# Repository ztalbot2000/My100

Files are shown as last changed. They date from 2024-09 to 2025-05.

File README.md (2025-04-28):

<div class="image123">
   <div style="float:left;margin-right:5px;">
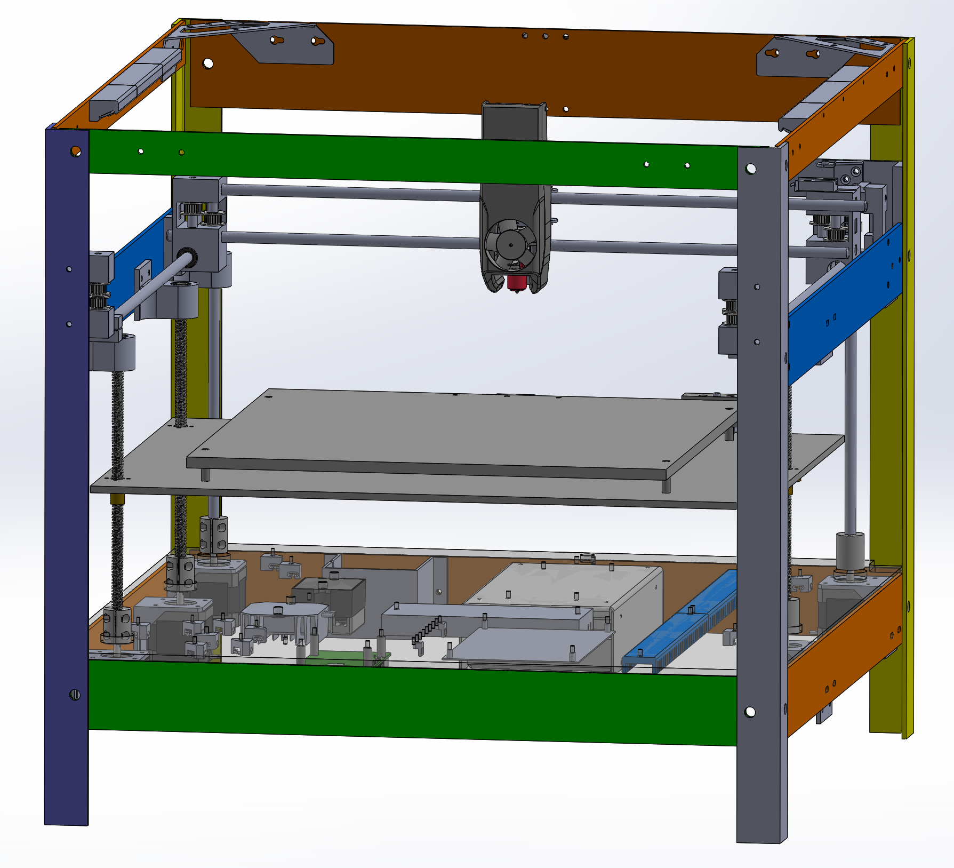
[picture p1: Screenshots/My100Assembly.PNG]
      
      <p style="text-align:center;">Latest Assembly Drawing</p>
   </div>
   <div style="float:left;margin-right:5px;">
      
      <p style="text-align:center;">Latest Build Progress</p>
   </div>
   <div style="float:left;margin-right:5px;">
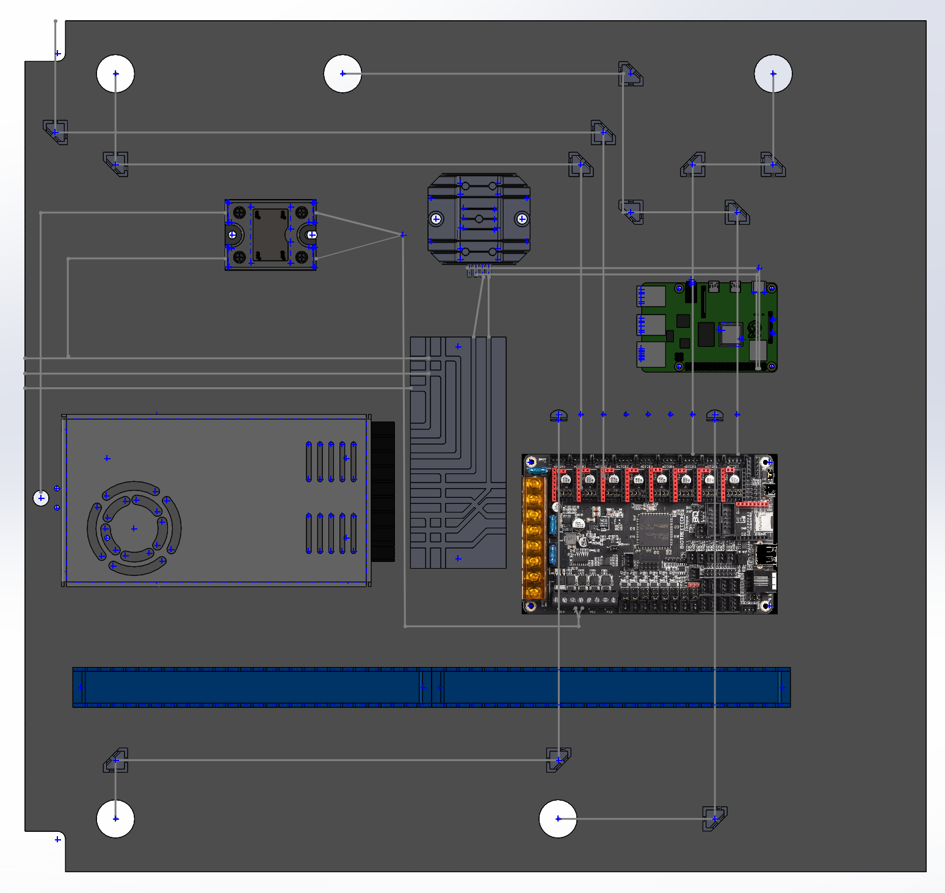
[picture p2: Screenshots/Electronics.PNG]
      
      <p style="text-align:center;">Latest Electronics Assembly Drawing</p>
   </div>
   <div style="float:left;margin-right:5px;">
      
      <p style="text-align:center;">Latest Electronics Build Progress</p>
   </div>
</div>

# My100 - A version of the100 with a metal frame.

<BR><BR>
## &nbsp;&nbsp;&nbsp; The **My100** is a meant to be built using common metal materials for a frame instead of the more expensive 20/20 extruded aluminum of the Voron or 3D printed frame of the100. This project is based primarily upon the great work of <A HREF="https://github.com/MSzturc/the100">the100</A>.
## &nbsp;&nbsp;&nbsp; BEWARE THIS WORK IS IN PROGRESS !! This is my second complete rebuild. The first failed quad gantry leveling so I decided to start again. You can see what I have created so far and are more than welcome to contribute. At the moment its just getting ready to try its first print. Wish me luck!
## &nbsp;&nbsp;&nbsp; Will the My100 be faster than the100, We shall see.

<BR><BR>
## Table of Contents
* [**My100 3D Printer Build Advantages**](#my100-3d-printer-build-advantages)
* [**Design Strategy**](#design-strategy)
* [***Imperial/Metric and Metal Thickness***](#imperialmetric-and-metal-thickness)
* [**SolidWorks 2023 Maker Edition and Equations**](#solidworks-2023-maker-edition-and-equations)
* [**Current Build Status My100 1.0 Alpha 7**](#current-build-status-my100-10-alpha-7)
* [**Current Build Status My100 1.0 Alpha 6**](#current-build-status-my100-10-alpha-6)
* [**Current Build Photos**](docs/CurrentBuildPhotos.md)
* [**ChangeLog**](CHANGELOG.TXT)
* [**Bill of Materials**](docs/My100BOM.md)
* [**Gotchas of building your own 3D printer**](docs/Gotchas.md)
* [**Contributing**](#contributing)

<BR><BR>
## My100 3D Printer Build Advantages
&nbsp;&nbsp;&nbsp; Here are some of what I believe to be My100 improvements.
<UL>
<LI>Use cheaper 6061 "L" shaped aluminum for the frame.
<LI>Wider 350 X 350mm build plate.
<LI>Keep threaded rod for Z-Axis so bed remains at height when powered off and is a less complicated assembly than gears/belts and pulleys.
<LI>Use 5mm steel shaft instead of M5 screws to support gantry bearings, eliminating noise and possible wear.
<LI>Use 20T pulley instead of F695 bearings. These seem to be higher quality. They run smoother around the 5mm steel shaft than a M5 machine screw.
<LI>All parts to be created are fully defined in SolidWorks and have been designed with equations.
<LI>Fastening holes for an enclosure is mandatory feature. Any fumes from a 3D printer should be externally vented as they are extremely harmful.
<LI>Build plate is 350 X 350mm. The height is at 200mm as I prove in the design, but is easily changed via equations of VSLength.
<LI>End stops and some sort of probe for bed leveling will be added as if you ever used a cheap 3D printer, leveling can be a nightmare.
<LI>Gantry steppers moved from within frame to electronics below so steppers will not be susceptible to heat issues.
</UL>
<BR><BR>

## Design Strategy
&nbsp;&nbsp;&nbsp; the100 is a great 3D printer otherwise I would not want to attempt to create one in the first place. It is also open source, as is the Voron. An inexpensive metal frame is the first goal.

&nbsp;&nbsp;&nbsp;20/20 extruded aluminum is expensive. Using more common 6061 "L" shaped aluminum is 50% cheaper. Just printing the100 with a 265x265mm bed was going to cost as of Oct 6/2023 $823 Cdn + tax. The aluminum for the frame of the My100 was $172 Cdn, including tax, plus $362 including tax for the Gantry blocks, larger 350 X 350mm bed, rod stabilizers and belt tensioners. Overall a much cheaper option with strength benefits. Further cost savings could be obtained if you created the bed out of metal too, but I splurged on a colorful bed.

&nbsp;&nbsp;&nbsp;Surprisingly, the ability to adjust location of parts is key and the primary reason for the second rebuild. Using ready mount stepper mounts turned out to be wiser than using the CNC to put the holes into the frame itself.

### Imperial/Metric and Metal Thickness
&nbsp;&nbsp;&nbsp;Important: In Canada metal is still purchased in Imperial units. While lengths can be obtained in Metric, the thickness would still be 1/8th inches (.125in). The .125in thickness is used throughout the design, but otherwise Metric is used.

<BR><BR>
## SolidWorks 2023 Maker Edition and Equations
&nbsp;&nbsp;&nbsp; SolidWorks Maker Edition is a fantastic tool and at $10 month its well worth it. You can stop the license at any time to save you money. I found it prettyy easy to use and there are so many tutorials out there.

### Globals WorkAround
&nbsp;&nbsp;&nbsp;There is one issue I have with the SolidWorks Maker edition and that is it does not include support for global variables being read in from a file for multiple parts. This is extremely annoying as many parts share the same equations when calculating the position of corresponding holes.

&nbsp;&nbsp;&nbsp;To that end I created a Node.js tool called <A HREF="https://github.com/ztalbot2000/SWECompare">SWECompare (SolidWoreks Equation Comparison)</A> to help with the task of having multiple parts use the same equations. 
<BR>

### Understanding the Equations
&nbsp;&nbsp;&nbsp;To change the dimensions of this 3D printer or to know how it was designed, you must understand the underlying equations.

#### Vertical alignment
&nbsp;&nbsp;&nbsp;Each component is stacked relative to the other, in the following manner.

<UL>
<LI>Electronics below the lower rail.
<LI>The length of the Z-Axis threaded rods at the end of the steppers.
<LI>The bed at the top of the Z-Axis.
<LI>The build plate on top of the bed.
<LI>The tip of the hotend on the build plate equal to the build plate on top of the bed.
<LI>The middle of the top the X-Axis rod from the hot end tip..
<LI>The middle of the Y-Axis rod from the middle of the X-Axis rod.
<LI>The middle of the X-Axis rod to the top pulley of the gantry.
</UL>

#### Left to Right Alignment.
&nbsp;&nbsp;&nbsp;It is not the build plate that dictates the width but the length of the X-Axis linear rod so it fits between the left and right gantry blocks. The bed and build plate are then centered between the steppers in this direction.

#### Front to Back Alignment
&nbsp;&nbsp;&nbsp;The front steppers for the Z-Axis are by the belt tensioners. The build plate size dictates everything else. Similiarly the Y-Axis linear rail placement traverses the length of the build plate so that the hot end tip can reach the whole area.

<BR><BR>
## Current Build Status My100 1.0 Alpha 7
(In progress)
<UL>
   <LI> Bed Mesh works
   <LI> Added larger Z endstop switch
   <LI> Moved gantry steppers to electronics below.
   <LI> Moved drag chain to middle of hot end carrier to remove the possability of any lever affect to the hot end.
   <LI> Trying to print... Oooooh
</UL>

<BR><BR>
## Current Build Status My100 1.0 Alpha 6
<UL>
   <LI>CAD design is complete.
   <UL>
      <LI>I was smarter in using rods as Matt pointed out when he had seen my first designs to solve flexing issues.
      <LI>Moved to Z-Tilt instead of QGL. Trying to level a four legged chair is not ideal.
      <LI>Connection points use one 8mm screw to allow for racking adjustments.
      <LI>Steppers are mounted with brackets and a slot for adjusting.
   </UL>
   <LI> Drag chains added. (Not in CAD design yet)
   <LI> Disco lights added.
   <LI> Build is complete.
   <LI> Wiring is tested. All motors move appropriately.
   <LI> All axis home.
   <LI> Automatic bed leveling complete. This was the fault with the previous design.
   <LI> Hot end heats up.
   <LI> Bed heats up.
   <LI> Working on Tidying up build, Tuning klipper config under RatOS 1.20.
</UL>

<BR><BR>
## Contributing
&nbsp;&nbsp;&nbsp; Best ways to contribute
* Star it on [GitHub](https://github.com/ztalbot2000/My100) - if you use it and like it please at least star it :)
* Follow the repo on [GitHub](https://github.com/ztalbot2000/My100)
* Follow me [ztalbot2000](https://github.com/ztalbot2000)

<BR><BR>
## Inspiration and special thanks
Based on :
* [the100]https://github.com/MSzturc/the100
* Thanks especially to those who continue to work on the100 and those who make it better.
* And most importantly my Wife.

<BR><BR>
## License
See [LICENSE](LICENSE)

<!---
Link References (Not Local)
-->

[ncviewer]:https://ncviewer.com
[viewstl]:https://viewstl.com/classic/
[Clicky Installation]:https://3dpblog.com/klicky-probe-installation-voron/
[BLTouch Installation]:https://www.klipper3d.org/BLTouch.html
[Ratrig v-core-3]:https://docs.ratrig.com/product-details/v-core3-1
[Heater Pad installation]:https://www.youtube.com/watch?v=RnCW7-_G2dI
[Heater Pad installation]:https://www.youtube.com/watch?v=-fMPnBuyxy8
[Heater Pad installation]:https://www.youtube.com/watch?v=BE1rW7XyXqw
[Heater Pad installation]:https://www.youtube.com/watch?v=yhzWj-oaikk
[Hot End Wiring Guide]:https://docs.ldomotors.com/en/voron/voron2/wiring_guide_rev_c
[Understanding End Stops]:https://www.youtube.com/watch?v=Q2uBK5XzX4I
[Macros - Ellis Tuning Guide]:https://ellis3dp.com/Print-Tuning-Guide
[Disco on a Stick]:https://github.com/VoronDesign/Voron-Hardware/tree/master/Daylight/Disco_on_a_stick
[Bigtree Octopus v1 prep and wiring]:https://www.youtube.com/watch?v=_4YpUzo18Lc
[ztalbot2000]:https://github.com/ztalbot2000

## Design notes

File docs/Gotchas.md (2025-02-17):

<p align="center">
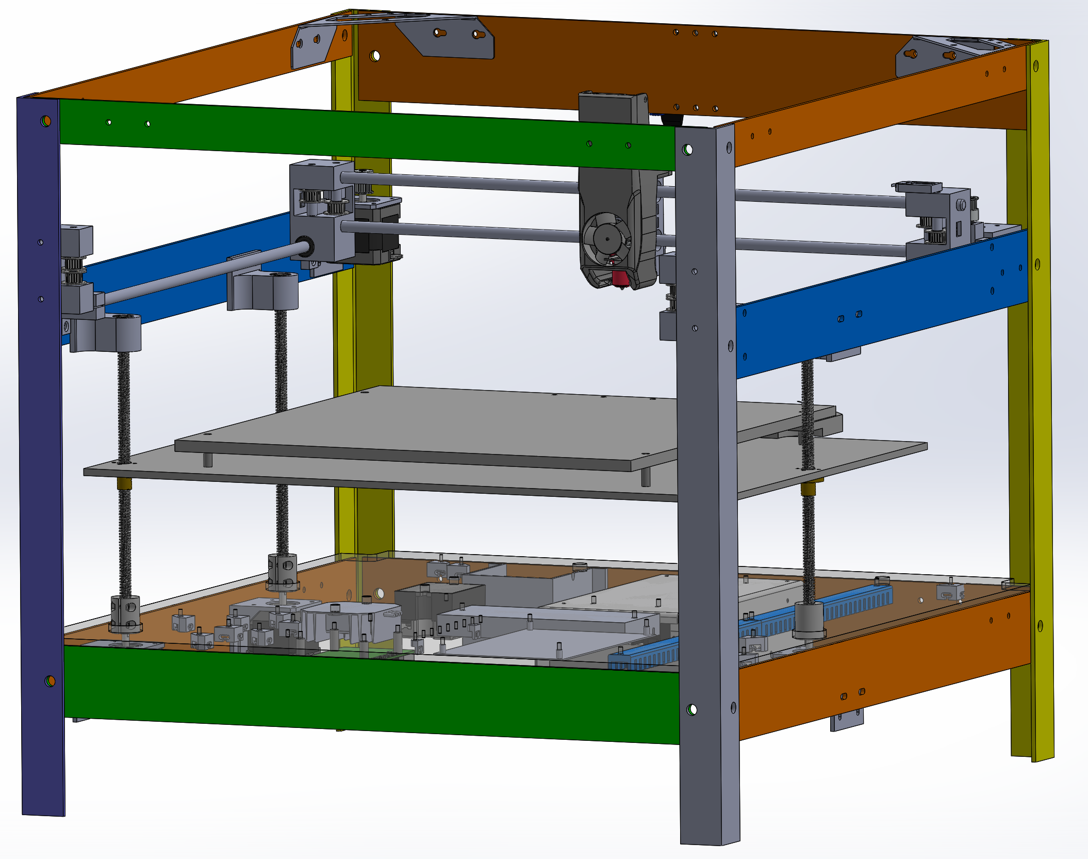
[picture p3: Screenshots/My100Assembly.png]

</p>

# These are a list of things I learned the hard way about building a 3D printer; So even if you do not build this printer, but decice to build your own, these are things to look out for.

## Leasons learned the hard way, that may not be so obvious.
<UL>
<LI> Many control boards with the same version number have different versions of STM32 controller chips. Understand and even try to compile the firmware for the control board you intend to buy. Take into consideration which stepper drivers you will be using as some firmware and even OS's say they support TMC2208 stepper drivers but only work with TMC2209. Prototyping just the controller with steppers and stepper drivers and getting them controlled by the OS of your choice will save you a lot of time and you may even understand the complexity of the whole project..
<LI> The more you design in SolidWorks, the less iterations you will have to build.
<LI> You need a 3D printer to build a 3D printer. Buying a cheap one is cheaper than having your parts printed. You will also learn how a 3D printer works and the pitfalls of a cheap one too.
<LI> JST-XH connectors are very tiny. Buy a good crimping tool and practice practice practice.
<LI> Buying steppers with connectors built into them will save you crimping some of the tiny JST-XH connectors.
<LI> A large 3D printer seems like the way to go, but it is correct that most things you will want to print can be done on a 235x235mm printer.
<LI> CoreXY printers do not have an X stepper and Y stepper because both steppers are needed to move the hot end in a single direction.
<LI> Quad Gantry Leveling refers to 4 point leveling where Z-Tilt referes to 3 points.
<LI> Trying to save money by putting the mounting holes directly into "L" shaped aluminum seemed like a good idea, but does not allow you to adjust the positioning later.
</UL>

<BR><BR>
## Wiring Gotchas
<UL>
<LI> I'll repeat this again. CoreXY printers do not have an X stepper and Y stepper because both steppers are needed to move the hot end in a single direction. So the steppers are actually Gantry Left and Gantry Right. Gantry left is Motor 1 and Gantry Right is Motor 0. Klipper still refers them to as stepper_x and stepper_y as Klipper supports many different 3D printer motion movement, but they are actually Gantry Right and Gantry Left.
</UL>

<BR><BR>
## License
See [LICENSE](../LICENSE)

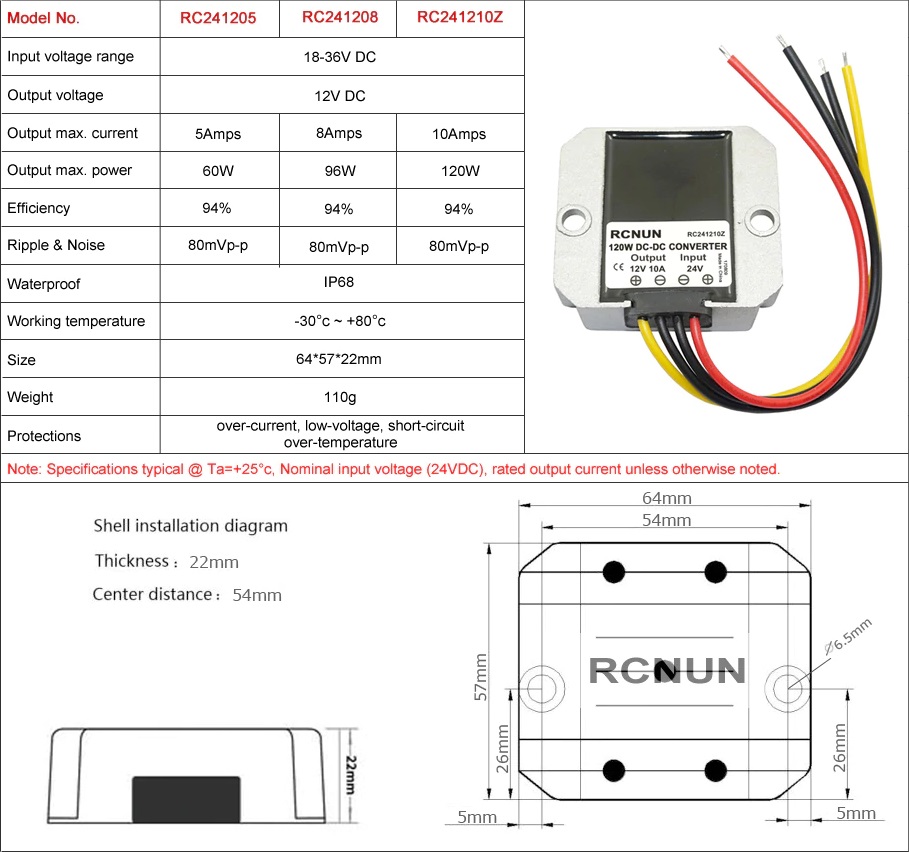
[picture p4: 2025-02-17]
SLD/AcquiredParts/RCNUN/RC2412 Spec.jpg

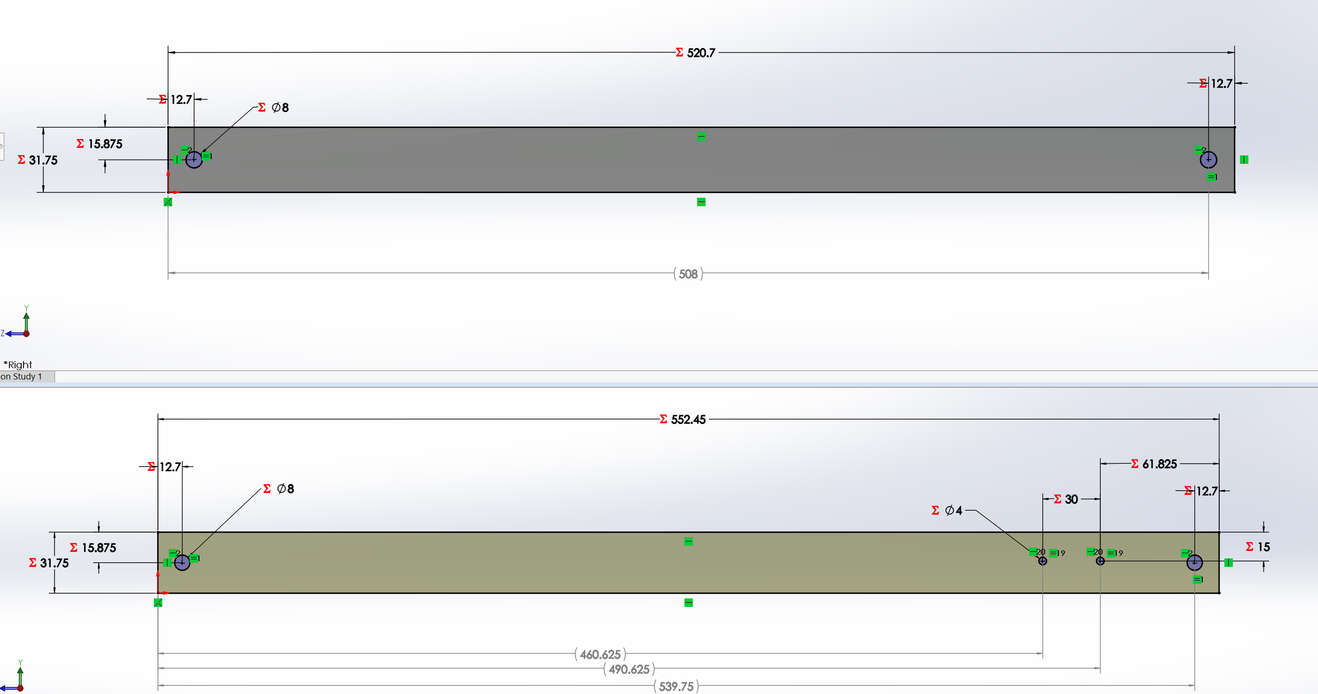
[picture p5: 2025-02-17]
Screenshots/Dimensions/UpperRails.PNG

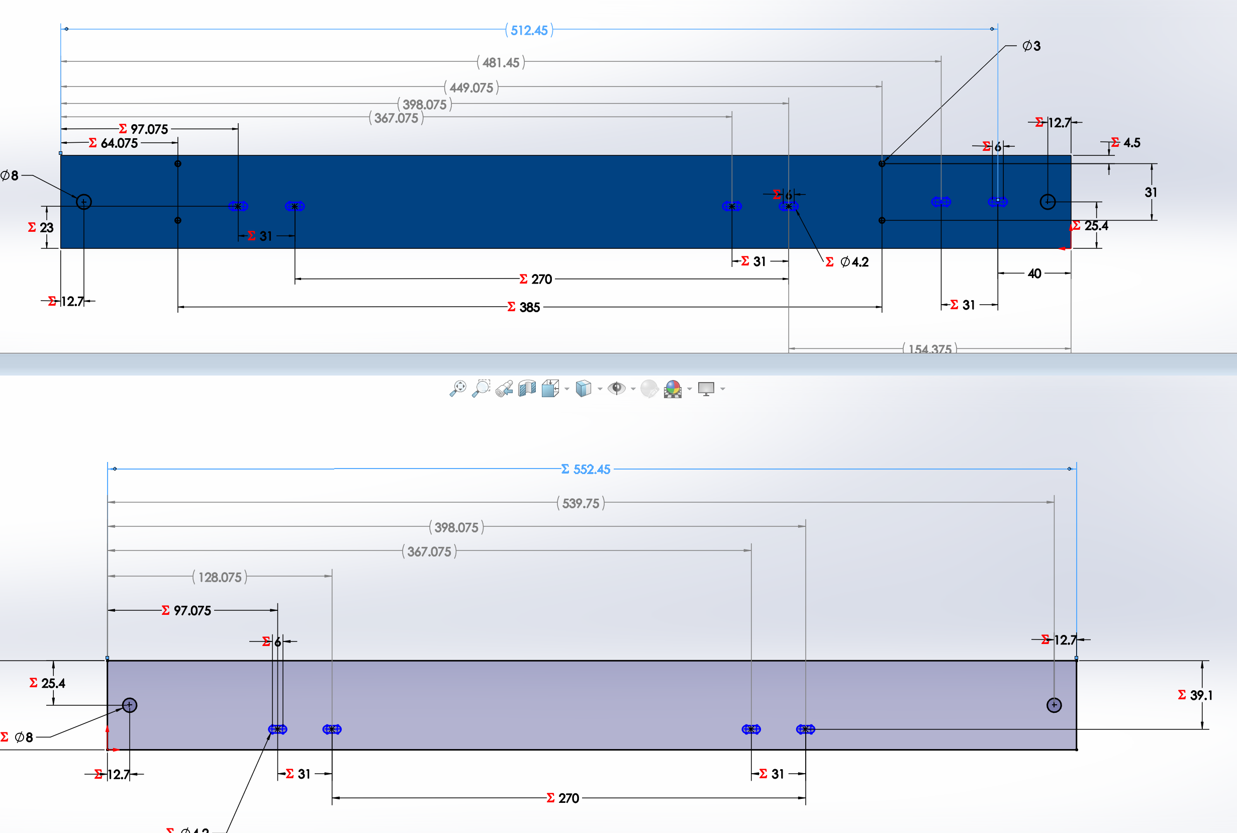
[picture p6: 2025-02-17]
Screenshots/Dimensions/LeftRails.PNG

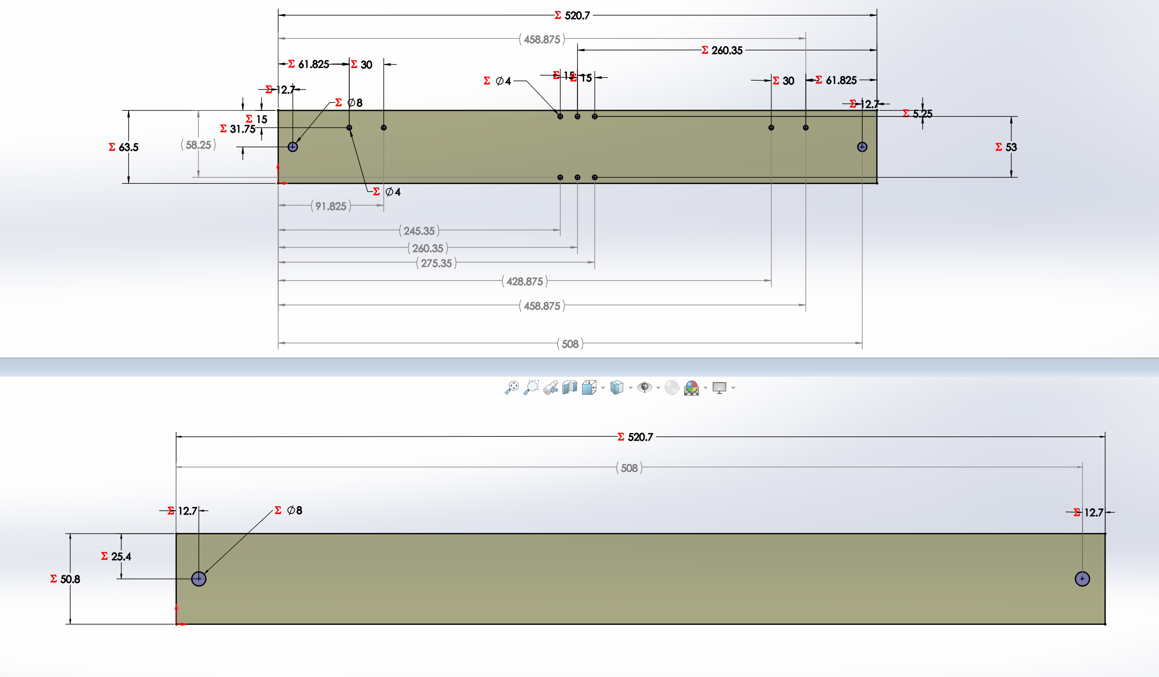
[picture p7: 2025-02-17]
Screenshots/Dimensions/FrontBackRails.PNG

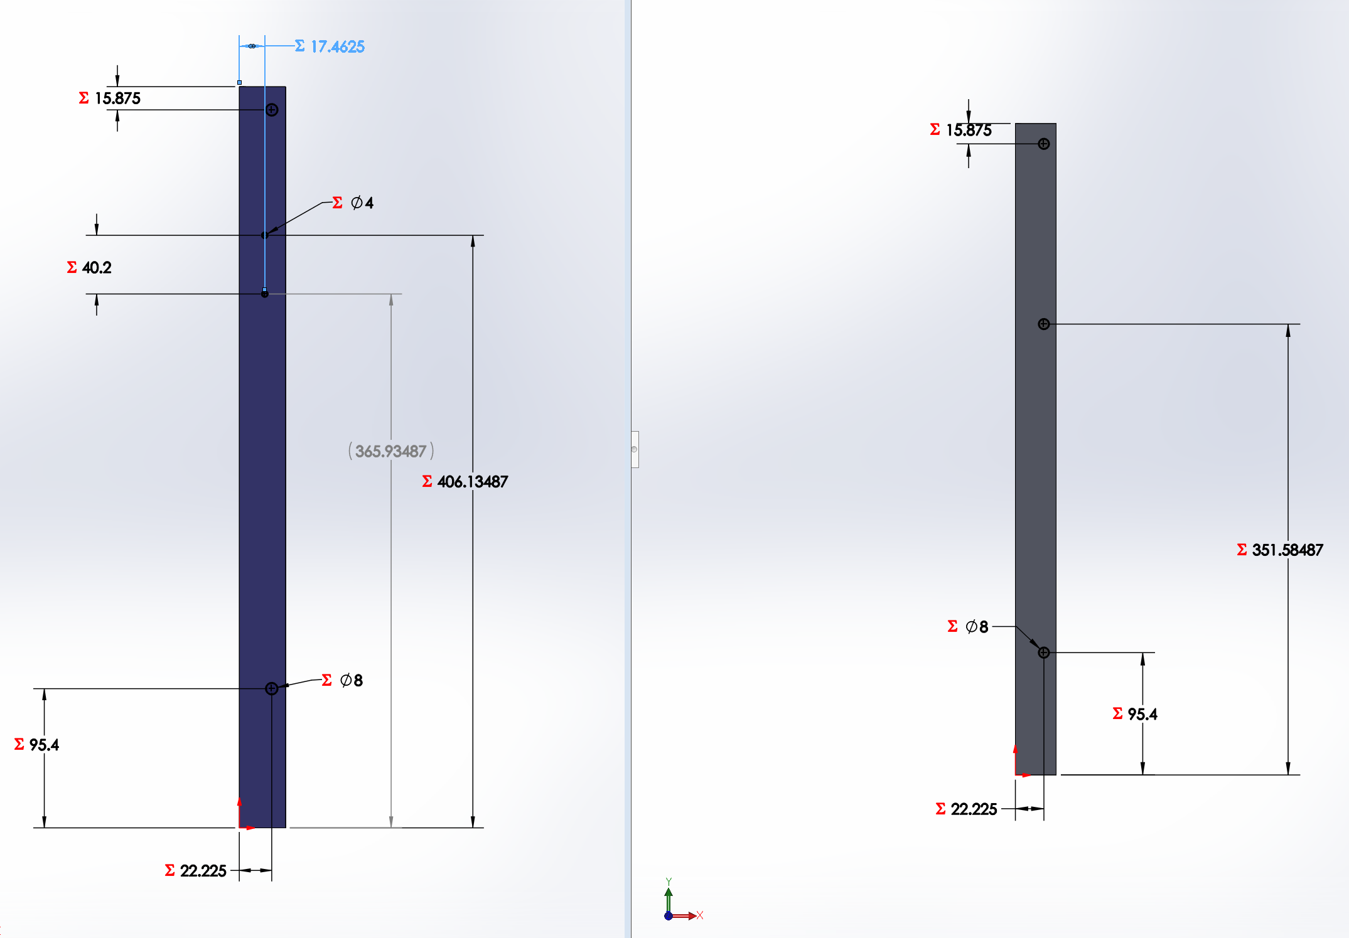
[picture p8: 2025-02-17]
Screenshots/Dimensions/FrontVS.PNG

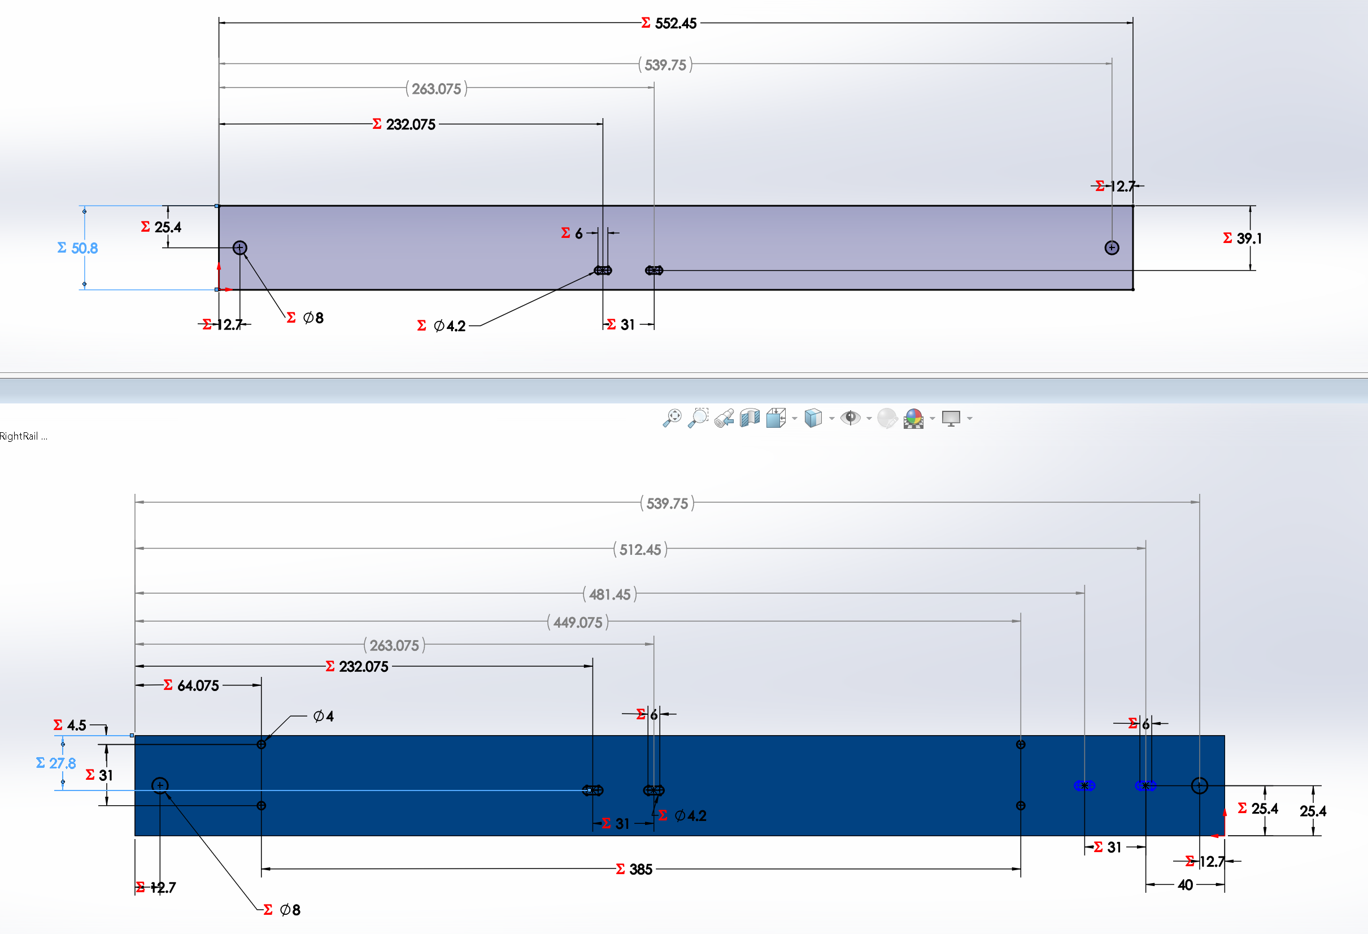
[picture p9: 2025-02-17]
Screenshots/Dimensions/MidRightAndRightLowerRails.png

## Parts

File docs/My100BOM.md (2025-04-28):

<HTML>
   <HEAD></HEAD>
   <BODY>
      <H1>Bill of Materials that differ from the100</H1>
      <TABLE>
         <HR><TD>Part<TD>Quantity<TD>Price (CDN)<TD>URL<TD>Purpose</HR>
         <TR><TD>Steel Shaft 5mm - 30mm<TD>6<TD>$2.95 each<TD>https://www.3dlabtech.ca/product/steel-shaft-5mm/<TD></TR>
         <TR><TD>Silicone Heater Mat 300mmx300mm-650w<TD>1<TD>$64.95<TD>https://www.3dlabtech.ca/product/silicone-heater-mat/<TD></TR>
         <TR><TD>PCB Klicky Probe kit<TD>1<TD>$29.95<TD>https://www.3dlabtech.ca/product/pcb-klicky-probe-kit/<TD></TR>
         <TR><TD>RJ4JP-01-08 Drylands<TD>4<TD>$4.58<TD>https://s.click.aliexpress.com/e/_DkZVosj<TD></TR>
         <TR><TD>Smooth Idler 6mm wide<TD>8<TD>$4.45 each<TD>https://www.3dlabtech.ca/product/smooth-idler-6mm-wide/<TD></TR>
         <TR><TD>Voron Trident Cast Aluminum 8mm Build Plate - 350x350mm<TD>1<TD>$164.95<TD>https://www.3dlabtech.ca/product/smooth-idler-6mm-wide/<TD></TR>
         <TR><TD>6-32 x 5/8 standard screws<TD>104<TD>$.05<TD><TD>Frame fastener</TR>
         <TR><TD>6-32 nuts<TD>104<TD>$.05<TD><TD>Frame fastener</TR>
         <TR><TD>6-32 lock washer<TD>104<TD>$.05<TD><TD>Frame fastener</TR>
         <TR><TD>M3 x 8 standard screw<TD>8<TD>$.15<TD><TD>Y axis guide block fastener</TR>
         <TR><TD>M3 x 8 pan head screw<TD>4<TD>$.15<TD><TD>Gantry rail clamp fastener</TR>
         <TR><TD>M3 x 20 standard head screw<TD>4<TD>$.15<TD><TD>X Axis guide block fastener</TR>
         <TR><TD>M4 x 25 standard head screw<TD>4<TD>$.15<TD><TD>Belt tightener fastener screws</TR>
         <TR><TD>M4 nylon nut<TD>4<TD>$.15<TD><TD>Belt tightener fastener screws</TR>
         <TR><TD>6-32 x 5/8 Cap Screw Socket Head<TD>14<TD>$.10<TD><TD>Bottom Frame Enclosure screws</TR>
         <TR><TD>6-32 Nylon Insert Hex lock nuts<TD>1<TD>$16.81 per 110<TD>https://www.amazon.ca/dp/B0CFHSM134?ref=ppx_yo2ov_dt_b_product_details&th=1<TD>Bottom Frame Enclosure screws</TR>
         <TR><TD>M6x16 Bolt<TD>2<TD>$.35 each<TD><TD>24v to 5V Power converter mounting bolts</TR>
         <TR><TD>M6 Nylon nut<TD>2<TD>$.30 each<TD><TD>24v to 5V Power converter mounting nuts</TR>
         <TR><TD>M4x10 Socket Cap screws<TD>4<TD>$.35 each<TD><TD>24v Power Supply mounting screws</TR>
         <TR><TD>Nema 17 42m Stepper Motor<TD>7<TD>$33.35 for 5<TD><TD></TR>
         <TR><TD>Mellow Hartk Sexbolt Z Limit Endstop Pcb Hardware Injection Kit Mod For Diy Voron 2.4 Trident 3D Printer<TD>1<TD>$12.28<TD>https://www.aliexpress.com/item/1005005910004587.html<TD></TR>
         <TR><TD>Disco on a Stick<TD>1<TD>$11.28 for 2<TD>https://www.aliexpress.com/item/1005005913975209.html<TD></TR>
      </TABLE>
   </BODY>
</HTML>

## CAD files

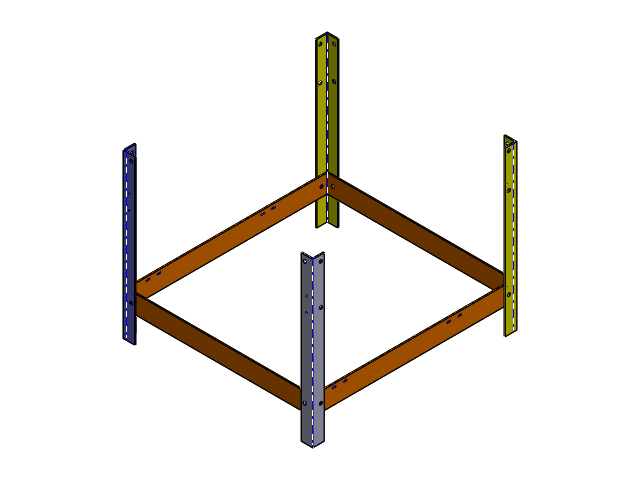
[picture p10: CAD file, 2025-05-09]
SLD/BottomFrame/My100LowerAssembly.SLDASM
FrontLeftVerticalSupport
LeftBeltTensioner
POWGE_2FT_pulley_20T_B5 x 4
7mmx1mmSpacer x 2
LowerFrontRail
FrontRightVerticalSupport
RightBeltTensioner
LowerRightRail
Nema17Mount x 5
LeadScrew 200mm x 8mm x 3
LeadScrew Nut 8mm x 2mmPitch x 3
Coupler x 5
Frontplate x 5
Backplate x 5
Connenctor x 5
Housing x 5
Bearing dummy x 5
Bearing dummy 01 x 5
Core x 5
Cable x 5
M3x34-Screw x 20
RodShaft-250mmx8mm x 2
GT2 Timing Pulley x 2
BackRightVerticalSupport
LowerBackRail
AC Power Inlet
PowerSwitchCover
BackLeftVerticalSupport
LowerLeftRail

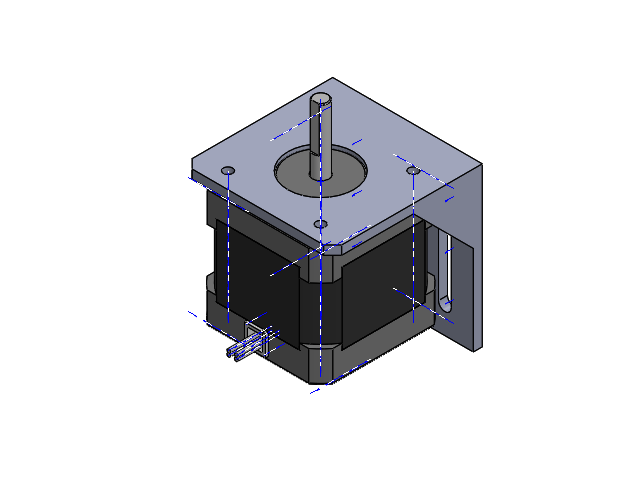
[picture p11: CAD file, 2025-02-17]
SLD/FromThe100/NEMA17-40/Nema17-40WithMountBracketAssembly.SLDASM
Nema17Mount
Frontplate
Backplate
Connenctor
Housing
Bearing dummy
Bearing dummy 01
Core
Cable
M3x34-Screw x 4

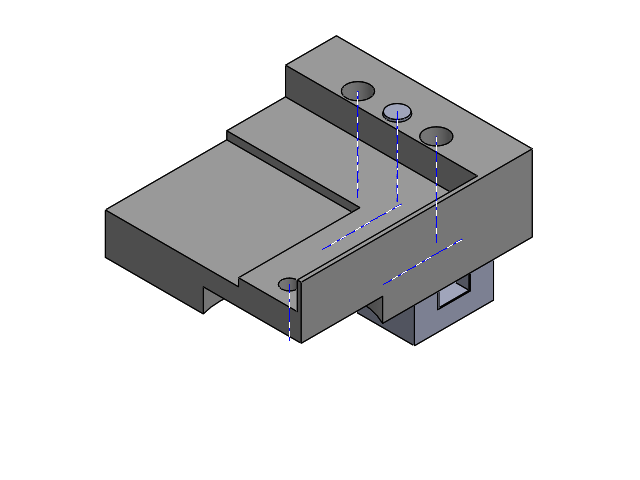
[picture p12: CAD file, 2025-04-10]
SLD/Bed/BuildPlateZEndStopHolderAssembly.SLDASM
BuildPlateZEndStopSwitchHolder
ZEndStopLimitSwitch

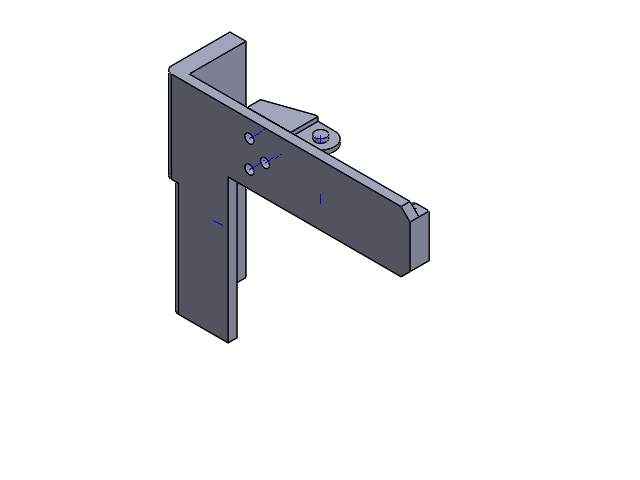
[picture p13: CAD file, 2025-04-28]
SLD/Extras/DragChainHangerAssembly.SLDASM
DragChainHanger
DragChainEndLinkMale

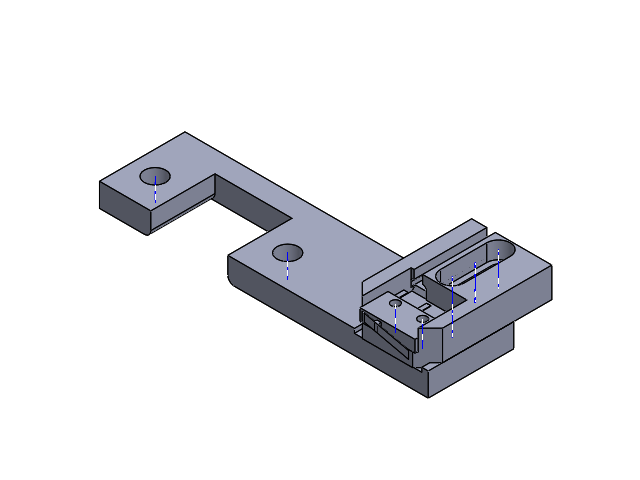
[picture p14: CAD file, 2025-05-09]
SLD/Gantry/YEndStopForRightRearSK8RodHolderAssembly.SLDASM
YAxisEndStopMicroSwitchHolder
MicroSwitch
YAxisEndStopBaseForRightRearSK8RodHolder

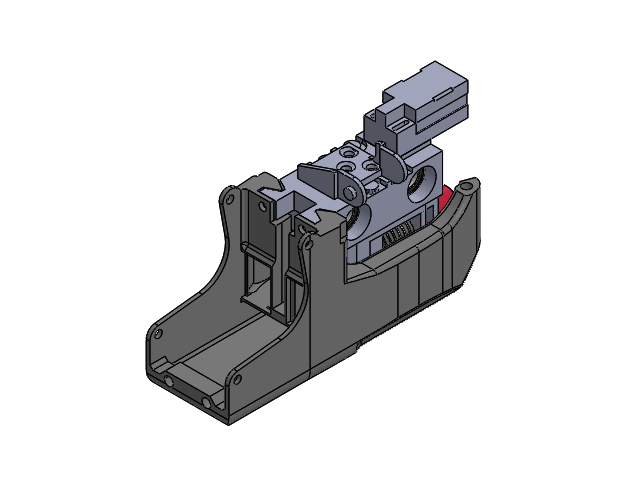
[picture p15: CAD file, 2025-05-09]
SLD/Hotend/HotEndAssembly.SLDASM
Heater
Arm
Sock
Screw_1
Hotend
Clip
Top_1
Screw
0.4 TUN Nozzle
CHC Pro Mount-17
CHC Pro Mount-18
4010 Fan Axial
Fanhead-19
CHC Mount
Carrier
InductiveProbe
LM8UU x 2
DragChainEndLinkRotatedMale

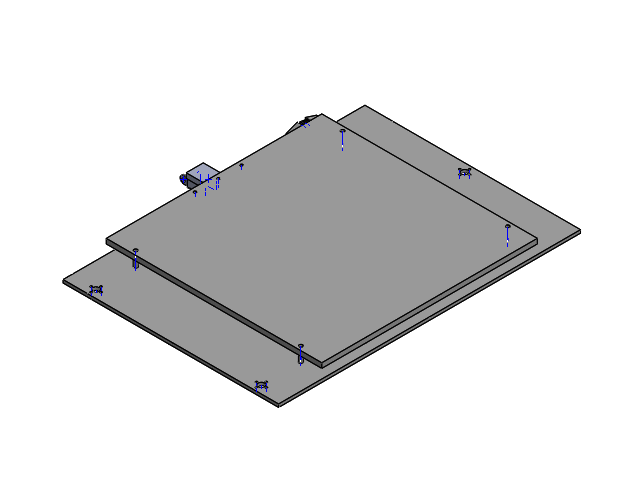
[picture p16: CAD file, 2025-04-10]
SLD/Bed/BedAssembly.SLDASM
Bed
Spacer 15mm x 4
BuildPlate
BuildPlateZEndStopSwitchHolder
ZEndStopLimitSwitch
DragChainBuildPlateConnector
DragChainBuildPlateConnectorTop
DragChainEndLinkMale

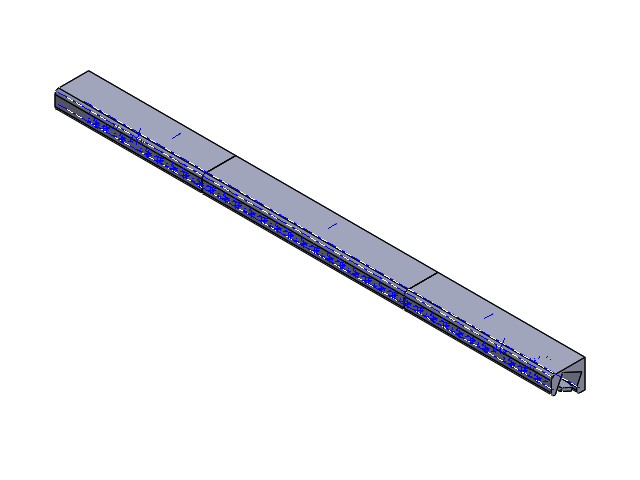
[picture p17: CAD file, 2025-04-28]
SLD/Extras/LeftLightGuideAssembly.SLDASM
LeftSideBackEndLightingGuide
MiddleLeftLightingGuide
LeftSideFrontEndLightingGuide
SOLID.step x 15
SOLID-0.step x 18
SOLID-1.step
PCB.step

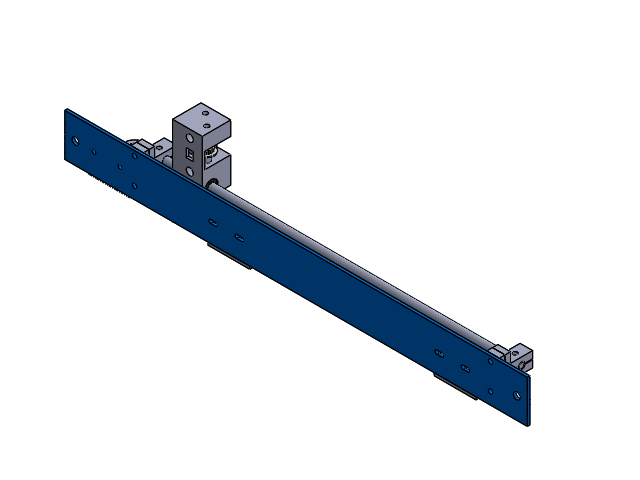
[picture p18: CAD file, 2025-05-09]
SLD/Gantry/MidLeftRailAssembly.SLDASM
MidLeftRail
SK8LinearShaftSupport x 2
RodShaft-440mmX8
LeftGantryBlock
POWGE_2FT_pulley_20T_B5 x 2
LM8UU x 4
RodStabilizer x 3
SK8Riser x 2

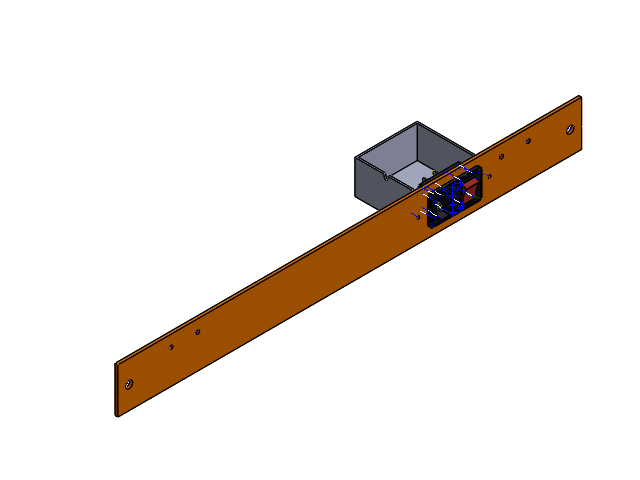
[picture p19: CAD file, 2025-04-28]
SLD/BottomFrame/LowerBackRailAssemblly.SLDASM
LowerBackRail
AC Power Inlet
PowerSwitchCover

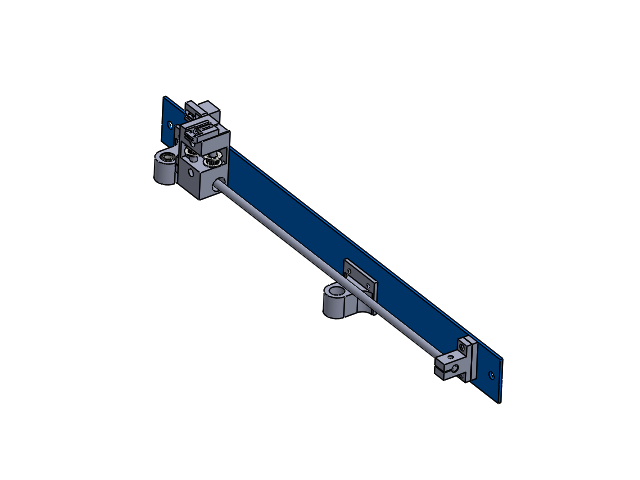
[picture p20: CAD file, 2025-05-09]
SLD/Gantry/MidRightRailAssembly.SLDASM
MidRightRail
SK8LinearShaftSupport x 2
RodShaft-440mmX8
RodStabilizer x 2
RightGantryBlock
POWGE_2FT_pulley_20T_B5 x 2
MicroSwitch x 2
YAxisEndStopMicroSwitchHolder x 2
LM8UU
YAxisEndStopBaseForRightRearSK8RodHolder
SK8Riser

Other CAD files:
SLD/FromThe100/Left Gantry Block/F695 Umlenkrolle_2.SLDASM
SLD/FromThe100/24VPSU/24V15A.SLDASM
SLD/FromThe100/Right Gantry Block/F695 Umlenkrolle_1.SLDASM
SLD/FromThe100/5mm - 8mm Coupler.SLDASM
SLD/FromThe100/CHCToolHeadAssembly/Rod Carriage.SLDASM
SLD/FromThe100/Extruder/NEMA17-40_4.SLDASM
SLD/FromThe100/Right Gantry Block/Right Gantry v1.SLDASM
SLD/AcquiredParts/AngleBracket.SLDPRT
SLD/AcquiredParts/BuildPlate.SLDPRT
SLD/AcquiredParts/CWD4890-Crydom/CWD4890 - CRYDOM.SLDPRT
SLD/AcquiredParts/CWD4890-Crydom/CWD4890 - CRYDOM.x_t
SLD/AcquiredParts/Daylight_Disco/Daylight_Disco.SLDASM
SLD/AcquiredParts/Daylight_Disco/Daylight_Disco.step
SLD/AcquiredParts/GT2_Pulley_20T_8mmBore/GT2 Timing Pulley.SLDPRT
SLD/AcquiredParts/InductiveProbe.SLDPRT
SLD/AcquiredParts/MicroSwitch.SLDPRT
SLD/AcquiredParts/Nema17Mount.SLDPRT
SLD/AcquiredParts/POWGE_2FT_pulley_20T_B5.SLDPRT
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

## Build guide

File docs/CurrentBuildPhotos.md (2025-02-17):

# These are all the photos from the scrapped build.

# Current Build Photos
&nbsp;&nbsp;&nbsp; There are a number of pictures that will be posted here as the My100 becomes a reality.  As this is Alpha quality, buyer beware.

<BR><BR>
## Wiring
&nbsp;&nbsp;&nbsp; This is better than most wiring diagrams.<BR>



<BR><BR>
## Latest Assembly of the Frame
&nbsp;&nbsp;&nbsp; The main GitHub page now has this picture.<BR>



## The First Metal Frame CNC Photos
&nbsp;&nbsp;&nbsp; The frame is designed so that the drill holes can be made with a drill press as previously mentioned; However, since I have a large CNC that I built years ago, the following are the first images of the front side of the Front Left Vertical support being CNC'd.

<BR>
<BR>A wide view of the milled piece<BR>

<BR><BR>A close up view of the milled piece<BR>

<BR><BR>A wide view of the mill and bCNC<BR>


<BR><BR>
## The Belt Tensioners
&nbsp;&nbsp;&nbsp; The Belt Tensioners were printed.  It was easier to replicate the100 belt tensioners. Like the My100 Gantry, steal 5mm shafts were used and idler pulleys to decrease the noise I heard from just using M5 bolts..



<BR><BR>
## The Gantry Blocks
&nbsp;&nbsp;&nbsp; The Gantry Blocks were printed. This is in accordance with the100. Printing it reduces the weight which increases how fast the gantry blocks can be moved.



<BR><BR>
## The Metal
&nbsp;&nbsp;&nbsp; All but the mid rear rail has been cut to size here.



<BR><BR>
## License
See [LICENSE](../LICENSE)

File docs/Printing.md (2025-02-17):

<div class="image123">
   <div style="float:left;margin-right:5px;">
      
      <p style="text-align:center;">Latest Assembly Drawing</p>
   </div>
   <div style="float:left;margin-right:5px;">
      
      <p style="text-align:center;">Latest Build Progress</p>
   </div>
</div>

# My100 - Printing Notes. If you never printed anything before, or maybe even if you have you will learn that cheap Creality printers have a nickname of Cruality printers and for good reason.  This is not a Cruality printer but learning to print on my friends bad printer has made me come to understand some key concepts and tricks.

<BR><BR>
# Bed leveling
## &nbsp;&nbsp;&nbsp; Our bed leveling will be much more automatic than using leveling screws on each corner. Still though there is automatic leveling to detect any bed variances. Did you know you need to tell the printer to use these numbers on each run. In your slicer software, add the following to your startup gcode.
```text
;Use Bed Mesh saved in Slot #1
M420 S1
;Blend out any compensation of the mesh in the first 10 layers
Z10
```

<BR><BR>
# Slicer addjustemnts: Minimal support area.
## &nbsp;&nbsp;&nbsp; If you use supports, small holes get filled in unnecessarily. To stop this from occuring, change this slicer software parameter:

``` text
Minimal support area: 15.0 mm2
```

<BR><BR>
## License
See [LICENSE](LICENSE)

<!---
Link References (Not Local)
-->

[Hot End Wiring Guide]:https://docs.ldomotors.com/en/voron/voron2/wiring_guide_rev_c
[Afterburner toolhead board v3.2/4.0 Wiring diagram]https://www.teamfdm.com/forums/topic/163-afterburner-toolhead-board-v3240-wiring-diagram-for-btt-octopus-1x-mcu/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
[ztalbot2000]:https://github.com/ztalbot2000

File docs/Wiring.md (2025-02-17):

<div class="image123">
   <div style="float:left;margin-right:5px;">
      
      <p style="text-align:center;">Latest Assembly Drawing</p>
   </div>
   <div style="float:left;margin-right:5px;">
      
      <p style="text-align:center;">Latest Build Progress</p>
   </div>
</div>

# My100 - Wiring Diagrams. Most of the wiring is similiar to the Voron 2.4 as it uses the same Octopus v1.1 control board. These notes are just clarification to where I found things confusing or different.

<BR><BR>
# Motor Wiring
## &nbsp;&nbsp;&nbsp; I got very confused with the labelling of the stepper motors on the Voron and the Octopus v1.1. The main thing to note is that the motor numbers start from zero and there are 2.1 and 2.2 motors for two extruders. Otherwise the voron documentation is correct.

<BR><BR>
# Hot End Wiring
## &nbsp;&nbsp;&nbsp; The hot end cable harness labels may be confusing.
XES - X End Stop<BR>
YES - Y End Stop<BR>
CT  - Chamber Thermistor<BR>
THO = HT - Hot End Thermistor<BR>
Connecting the +24V wire to the heater terminal (Rather than the the PSU) means its protected by the fuse on the board.
PCF - Print/Part Cooling Fan
HEF - Hot End Fan
<BR>
See: https://docs.vorondesign.com/build/electrical/v1_octopus_wiring.html

<BR><BR>
# Probe Wiring
## &nbsp;&nbsp;&nbsp; Inductive Probe
I found this article interesting recommending changes for drift and back EMF.<BR>
https://www.reddit.com/r/VORONDesign/comments/xo3475/voron_24_instructions_inductive_probe_need/<BR>
With that in mind you need to change the octopus probe output voltage to 12v, which means that on
https://docs.vorondesign.com/build/electrical/v2_octopus_wiring.html do not do step 5, Inserting the jumper into V_FUSED to set the probe voltage to the system supply voltage. Where it is red in the diagram is the correct position for 12v.

<BR><BR>
## License
See [LICENSE](LICENSE)

<!---
Link References (Not Local)
-->

[Hot End Wiring Guide]:https://docs.ldomotors.com/en/voron/voron2/wiring_guide_rev_c
[Afterburner toolhead board v3.2/4.0 Wiring diagram]https://www.teamfdm.com/forums/topic/163-afterburner-toolhead-board-v3240-wiring-diagram-for-btt-octopus-1x-mcu/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
[ztalbot2000]:https://github.com/ztalbot2000

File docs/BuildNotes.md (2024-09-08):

Tne silicone heater matt with built in 120C thermal fuse was:
https://www.3dlabtech.ca/product/silicone-heater-mat/
Their notes say:
**Includes built in 120C thermistor fuse

A silicone heater mat is a great way to heat your 3D Printer build plate. Please make sure you select the right size of mat for your 3D printer.

All silicone heater mats include 3M 468MP 200MP adhesive backing so you can easily adhere the heater mat to the build plate. This adhesive is rated for temperatures up to 149C long term and 204C short term.
Silicone heater mat includes NTC 100k beta 3950 thermistor (use “Generic 3950” in config)
All our silicone heater mats are 110v AC
It is recommended to use High Temp RTV silicone around the edge of the silicone heater mat after installing on the build plate as a safety measure during installation. This will ensure the heater mat never falls off the build plate.
Red wires are for thermistor
White wires are power wires for the heater element

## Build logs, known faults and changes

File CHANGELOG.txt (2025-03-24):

This will be an incomplete change log until further notice.

v1.0Alpha-6 (Rebuild checkpoints)
===========
- Lets just say that so far this was a total rebuild to fix bed leveling.
There are too many things to list that were done. I'm now past the stage of
testing bed leveling as was in the previous release that failed.

v1.0Alpha-5 (Will start over because of QGL failing )
===========
- Will try to update CAD drawings and create a video of what is operational.
- Backed out LeftGantryBlock X stop as it does not touch hot end to trigger
it.
- Moved Z stop on RodStabilizer to right side so when it is moved to back
right it will trigger.
- Changed build plate to M4 screw size on each corner for move to
shortBedSupport.
- Added bedAssembly2, which will be a newer bed assembly. Still not sure about
this.
- Modified X & Y endstops for better fit.
- Added Probe holders. Not sure if I'll use Inductive or BLTouch. Inductive
  seems easier to configure.
- Removed M3 heat insert hole for LM8UU fastener and replaced it with block
  at bottom of RodStabilizer to remove any possible tightness on the LM8UU
  to the 8mm screw.
- Shrunk size of RodStabilizer front to size of LM8UU only.
- Stupid build plate is not 350x350 but 352x352mm.
- Changed bed to be aluminum as printed base was to flimsy and levers caused
  to much stress on the Z Axis threaded rods. At least this is what I believed
  was causing QGL to fail.

v1.0Alpha-4
===========
Note: The electronics will continue from Alpha-3. I actually have gantry
moving.!!!
There are some design changes I want to make that may only be refeclected
in the build much later. Specifically orientating the X-Axis so that the Hot
End faces backwards. This will potentially allow multiple Hot Ends to handle
multiple colors.

- Updated wiring clamps and created a endstop wiring clamp.
- Created a Gotcha document. If you build any 3D printer on your own, this
  would have been nice to know first.
- Need to create documentation on how to compile Marlin for components used.
- Steppers are operational.
- Had fun trying to figure out RATOS, Pronterface, OctoPi. Klipper and Marlin
  trying to get steppers tested. Most tools think you must have the printer
  fully assembled before it will move a stepper.
- Add drawio schematic. Duplicated some images, I should resolve this later.
- Add in Wiring clamps, guides, grommets.
  HDMI and USBC connectors to go out the back (Elbows required).
- Add X Stop to rear left RodStabilizer. Not in main assembly yet.
- Change BeltFasteners to have more space for MidRail fasteners.
- Instead of large bed, create build plate lifters to each Z Axis rod.
  Not in main assembly yet.
- Add Z Stop to rear left RodStabilizer if Clicky not used. Not in main assembly yet.
- Reduce weight of Carrier.
- Mount X-Axis linear rail on its own printed bar so that the X-Axis is
  more rigid.
- Added endstops to bottom of Left Gantry block and left rear rod stabilizer.
  This is wrong and is being fixed as homing is back right.
- Added ball joint models for build plate to use short bed supports.
- This will all be merged as Alpha-4 but my actual build as many features yet
  not implemented in CAD.

v1.0Alpha-3 (Built, except Lower Rails re-used from Alpha 2)
===========
- Back Mid rail was rotated upside down so the steppers face upwards allowing
  their cables to be more easily routed and to shift center of mass lower.
- Modified belt fasteners to go around mid side rail mounting screws.
- Corrected bed parts to reflect their correct position relative to their
  part names.
- Changed bed center from solid to a shell, reducing material required to
  print it.
- Changed bed center overlap from filet to peg/hole connections to make it
  easier to assemble.
- Change RodStabilizer and Bed/Build Plate fastening holes to be M3 Heat
  insert diameter.
- Proof equations so that all parts that ribbon touch align exacly which was
  required after turning Mid Back rail upside down so steppers face upwards.
- Change four fastening holes to three to better accomodate screw heads.
- Add chamfer to fastening holes for screw heads on verticals.
- Add 24V DC to 5V DC converter onto enclosure bottom.
- Change to 1 foot mount hole on each side of vertical rail.
- Add fastening screws to frame.
- Move MidBackRail X&Y steppers forward to allow space for rear stepper screws.
- Add chamfer to corner of belt tensioners so they fit inside verticals.
- Add counter sink to gantry block mounting holes
- Increase size of Gantry block access holes.
- Add third Gantry block clamp hole for future X-Axis Linear Rail support.
- Add cable holes to lower frame

v1.0Alpha-2 (Altered from Alpha-1 build)
===========
- Change to three screws in each frame connection to avoid screw collisions.
- Increase diameter of BeltTensioner mounting hole.
- Add lower enclosure for mouting electronics.
- Remove lower corner gussets as no longer needed.
- Remove upper corner gussets as no longer needed.
- Add lower enclosure to mount electronics.
- Add mounting holes for PSU, Pi4 and Octopus V1,1 to lower enclosure.
- Change MidRail width from 1.25in to 2in for strength and allow
  for stronger Z-Axis rod stabilizers.
- Beef up Z-Axis rod stabilizers for future increase of Z-Axis length.
- Split assemblies so there is a MidFrame (Gantry) assembly.
- Create NC file for lower enclosure
- Add missing folder AcquiredParts
- Add PSU to assembly
- Add Pi4 to assembly
- Add OctopusV1.1 to assembly. Note: Step file is broken. Used a picture
  that mated to the enclosure instead of its standoffs.

v1.0Alpha-1
===========
This was actually built! Here are the things I would/did improve on
- I put 4 screw holes in each frame connection to the upper and lower
  rails. Three should be used as the inner most screws collide.
- The mid rail was made out of flat aluminum.  It bends to easily and
  should be made out of steel or 90 degree aluminum.
- The NC files are correct.  I did alter the feeds and Z-axis starting
  position and depths during the runs.
- During assembly, the rail corners needed to be filed to account for
  the 90 degree inside bead of the vertical supports.
- I used a 1/2 inch drill bit set to the appropriate depth on my drill
  press to make a chamfer that accommodates the head of a flat head machine
  screw.

v1.0Alpha-0 (Untagged)
======================
- The 3d printed base should not contain a 90 contour to mount the inner
  square as it causes the slicer to build a shelf to support it during
  printing.  This was changed to a 45 degree angle.

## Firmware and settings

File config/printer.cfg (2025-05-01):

#5 Voron 2.4 Klipper Config
# Documentation: https://os.ratrig.com

# The first thing you'll need to do is go through this file and comment out / uncomment
# the files and/or settings you need.
# You'll be able to print just fine with this config as it is, but it is recommended
# that you follow these steps to properly calibrate your printer:
# 0) Sanity check and PID Tuning: https://www.klipper3d.org/Config_checks.html
# 1) Pressure Advance: https://www.klipper3d.org/Pressure_Advance.html
# 2) Skew Correction: https://www.klipper3d.org/Skew_Correction.html
# 3) Resonance Compensation: https://www.klipper3d.org/Resonance_Compensation.html

# Read more about klipper here: https://www.klipper3d.org/Overview.html

[force_move]
enable_force_move: True

#############################################################################################################
### CONTROL BOARD
### Pick the board you have installed and wired in your printer.
#############################################################################################################
#[include RatOS/boards/btt-skr-pro-12/config.cfg]
[include RatOS/boards/btt-octopus-11/config.cfg]
[include RatOS/boards/btt-octopus-11-407/config.cfg]
#[include RatOS/boards/btt-octopus-pro-446/config.cfg]
#[include RatOS/boards/btt-octopus-pro-429/config.cfg]
#[include RatOS/boards/btt-octopus-pro-h723/config.cfg]
#[include RatOS/boards/btt-manta-m8p/config.cfg]
#[include RatOS/boards/btt-manta-m8p-11/config.cfg]
#[include RatOS/boards/fysetc-spider/config.cfg]

#############################################################################################################
### BASE SETUP
#############################################################################################################
[include RatOS/printers/v-core-3/v-core-3.cfg]
#[include RatOS/printers/voron-v24/voron-v24.cfg]
[include RatOS/homing.cfg]
[include RatOS/macros.cfg]
[include RatOS/shell-macros.cfg]
#Z [include RatOS/printers/voron-v24/macros.cfg]
# Same as voron-v24 except with z-tilt
[include RatOS/printers/v-core-3/macros.cfg]

#############################################################################################################
### STEPPER MOTORS, DRIVERS & SPEED LIMITS
### Pick the drivers and stepper motors you're using. See the RatOS documentation for custom combinations.
#############################################################################################################
# [include RatOS/printers/v-core-3/steppers.cfg]
# [include RatOS/printers/voron-v24/steppers.cfg]
# Removed Z3, No longer a Quad but a Tri
[include My100/My100Steppers.cfg]

####################
## UNCOOLED TMC 2209
####################
[include RatOS/printers/v-core-3/tmc2209.cfg]
# [include RatOS/printers/voron-v24/tmc2209.cfg]
# [include My100/My100tmc2209.cfg]
# [include RatOS/printers/v-core-3/speed-limits-basic.cfg]
[include RatOS/printers/voron-v24/speed-limits-basic.cfg]

# Singasong 5Pcs Nema17 Stepper Motor 17HS4401S 1.5A Nema 17 42BYGH 17HS4401 4 Lead for 3D Printer XYZ CNC Engraver

# LDO-42STH48-2004MAH on XY + LDO-42STH48-2004AC on Z
[include RatOS/steppers/ldo/42sth48-2004mah/2209/24v-0.8a-x.cfg]
[include RatOS/steppers/ldo/42sth48-2004mah/2209/24v-0.8a-y.cfg]
[include RatOS/steppers/ldo/42sth48-2004ac/2209/24v-0.8a-z.cfg]
[include RatOS/steppers/ldo/42sth48-2004ac/2209/24v-0.8a-z1.cfg]
[include RatOS/steppers/ldo/42sth48-2004ac/2209/24v-0.8a-z2.cfg]
# Removed Z3, No longer a Quad but a Tri
# [include RatOS/steppers/ldo/42sth48-2004ac/2209/24v-0.8a-z3.cfg]

# LDO-42STH48-2504AC on XYZ
#[include RatOS/steppers/ldo/42sth48-2504ac/2209/24v-1.1a-x.cfg]
#[include RatOS/steppers/ldo/42sth48-2504ac/2209/24v-1.1a-y.cfg]
#[include RatOS/steppers/ldo/42sth48-2504ac/2209/24v-1.1a-z.cfg]
#[include RatOS/steppers/ldo/42sth48-2504ac/2209/24v-1.1a-z1.cfg]
#[include RatOS/steppers/ldo/42sth48-2504ac/2209/24v-1.1a-z2.cfg]
#[include RatOS/steppers/ldo/42sth48-2504ac/2209/24v-1.1a-z3.cfg]


####################
## ACTIVELY COOLED TMC 2209
####################
# [include RatOS/printers/v-core-3/tmc2209.cfg]
# [include RatOS/printers/v-core-3/speed-limits-basic.cfg]

# LDO-42STH48-2004MAH on XY + LDO-42STH48-2004AC on Z
#[include RatOS/steppers/ldo/42sth48-2004mah/2209/24v-1.3a-x.cfg]
#[include RatOS/steppers/ldo/42sth48-2004mah/2209/24v-1.3a-y.cfg]
#[include RatOS/steppers/ldo/42sth48-2004ac/2209/24v-1.3a-z.cfg]
#[include RatOS/steppers/ldo/42sth48-2004ac/2209/24v-1.3a-z1.cfg]
#[include RatOS/steppers/ldo/42sth48-2004ac/2209/24v-1.3a-z2.cfg]
#[include RatOS/steppers/ldo/42sth48-2004ac/2209/24v-1.3a-z3.cfg]

# LDO-42STH48-2504AC on XYZ
#[include RatOS/steppers/ldo/42sth48-2504ac/2209/24v-1.6a-x.cfg]
#[include RatOS/steppers/ldo/42sth48-2504ac/2209/24v-1.6a-y.cfg]
#[include RatOS/steppers/ldo/42sth48-2504ac/2209/24v-1.6a-z.cfg]
#[include RatOS/steppers/ldo/42sth48-2504ac/2209/24v-1.6a-z1.cfg]
#[include RatOS/steppers/ldo/42sth48-2504ac/2209/24v-1.6a-z2.cfg]
#[include RatOS/steppers/ldo/42sth48-2504ac/2209/24v-1.6a-z3.cfg]

####################
## STEALTH MODE (Enables stealthchop and limits velocity and acceleration)
## NOTE: You still need to include one of the above stepper motor definitions.
## NOTE: This will make your printer quieter at low speeds but less accurate,
##       it's an inherent side effect of stealthchop.
####################
#[include RatOS/printers/voron-v24/tmc2209-stealth.cfg]


#############################################################################################################
### PHYSICAL DIMENSIONS
### Pick your printer size
#############################################################################################################
# Remove the # from your printer size below.
# Similarly add a # in front of [include RatOS/printers/voron-v24/300.cfg] if you have a bigger machine.
#[include RatOS/printers/voron-v24/250.cfg]
#[include RatOS/printers/voron-v24/300.cfg]
#[include RatOS/printers/voron-v24/350.cfg]
#[include RatOS/printers/v-core-3/400.cfg]
# Removed quad_gantry_level, No longer a Quad but a Tri
[include My100/My100350.cfg]


#############################################################################################################
### HOMING
### Pick your probe and endstops
#############################################################################################################
# Biqu probe
#[include RatOS/z-probe/biquprobe.cfg]
# BLTouch
#[include RatOS/z-probe/bltouch.cfg]
#[include RatOS/z-probe/microprobe.cfg]

# Inductive/Capacitive probe
[include RatOS/z-probe/probe.cfg]

# Euclid probe (please read the RatOS documentation for instructions)
#[include RatOS/z-probe/euclid.cfg]

# Klicky probe (please read the RatOS documentation for instructions)
#[include RatOS/z-probe/klicky.cfg]
#[include RatOS/z-probe/unklicky.cfg]

# Physical endstop on X
# [include RatOS/printers/v-core-3/physical-endstop-x.cfg]
[include RatOS/printers/voron-v24/physical-endstop-x.cfg]
# Physical endstop on Y
# [include RatOS/printers/v-core-3/physical-endstop-y.cfg]
[include RatOS/printers/voron-v24/physical-endstop-y.cfg]
# Physical endstop on Z, please comment out when using a Probe
# [include RatOS/printers/v-core-3/physical-endstop-z.cfg]
[include RatOS/printers/voron-v24/physical-endstop-z.cfg]

# Sensorless homing (Beware: this requires manual tinkering and does not work if your x/y stepper drivers
# have clipped DIAG pins). It is strongly encouraged to use physical endstops if you're a beginner.
# If you still wish to proceed, copy config/templates/sensorless-homing-tmc2209.cfg to the root directory and
# remove the # from the line below, then tune the settings in it, until you have reliable homing.
#[include sensorless-homing-tmc2209.cfg]

# If you want to only run sensorless homing on a single axis, copy the corresponding file from config/templates
# to the root directory and uncomment it below. Then tweak the settings in it until you have reliable homing.
#[include sensorless-x-homing-tmc2209.cfg]
#[include sensorless-y-homing-tmc2209.cfg]


#############################################################################################################
### INPUT SHAPER
### Enable/disable input shaper calibration
#############################################################################################################
# Uncomment this next line if you have an ADXL345 connected to your control board
#[include RatOS/printers/v-core-3/input-shaper.cfg]
#[include RatOS/printers/voron-v24/input-shaper.cfg]
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

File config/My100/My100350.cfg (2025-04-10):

# #Note: Taken from: v-core-3/300.cfg
# WARNING. DO NOT EDIT THIS FILE.
# To override settings from this file, you can copy and paste the relevant
# sections into your printer.cfg and change it there.

[stepper_x]
position_max: 350
position_endstop: 350

[stepper_y]
position_max: 350
position_endstop: 350

[stepper_z]
position_max: 310

[bed_mesh]
#   The speed (in mm/s) of non-probing moves during the calibration.
#   The default is 50.
speed: 50
# speed: 120 # As per video 
#   The height (in mm) that the head should be commanded to move to
#   just prior to starting a probe operation. The default is 5.
horizontal_move_z: 10  # See printer.cfg why we put this to 10.
#   Defines the minimum X, Y coordinate of the mesh for rectangular
#   beds. This coordinate is relative to the probe's location. This
#   will be the first point probed, nearest to the origin. This
#   parameter must be provided for rectangular beds.
# mesh_min: 20,20
# mesh_min: 30,30 # As per video
mesh_min: 30,0 # From z_tilt. Move out of range 30, -45
mesh_min: 30,40 # From z_tilt. Move out of range 30, -5
mesh_min: 30,45 # From z_tilt.
#   Defines the maximum X, Y coordinate of the mesh for rectangular
#   beds. Adheres to the same principle as mesh_min, however this will
#   be the furthest point probed from the bed's origin. This parameter
#   must be provided for rectangular beds.
# mesh_max:265,260
# mesh_max:315,260 # As per video
mesh_max:320,285 # From z_tilt
#   For rectangular beds, this is a comma separate pair of integer
#   values X, Y defining the number of points to probe along each
#   axis. A single value is also valid, in which case that value will
#   be applied to both axes. Default is 3, 3.
# probe_count: 7,7
probe_count: 3,3 # Creates 9 points
#   The gcode z position in which to start phasing out z-adjustment
#   when fade is enabled. Default is 1.0.
fade_start: 1.0
#   The gcode z position in which phasing out completes. When set to a
#   value below fade_start, fade is disabled. It should be noted that
#   fade may add unwanted scaling along the z-axis of a print. If a
#   user wishes to enable fade, a value of 10.0 is recommended.
#   Default is 0.0, which disables fade.
fade_end: 10.0
#   A comma separated pair of integers X, Y defining the number of
#   points per segment to interpolate in the mesh along each axis. A
#   "segment" can be defined as the space between each probed point.
#   The user may enter a single value which will be applied to both
#   axes. Default is 2, 2.
mesh_pps: 2,2
#   The interpolation algorithm to use. May be either "lagrange" or
#   "bicubic". This option will not affect 3x3 grids, which are forced
#   to use lagrange sampling. Default is lagrange.
algorithm: bicubic
#   When using the bicubic algorithm the tension parameter above may
#   be applied to change the amount of slope interpolated. Larger
#   numbers will increase the amount of slope, which results in more
#   curvature in the mesh. Default is .2.
bicubic_tension: .2

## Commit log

2023-11-11 feat:Initial commit
    [0.4 TUN Nozzle.SLDPRT, 4010 Fan Axial.SLDPRT, 5mm - 8mm Coupler.SLDASM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]
2023-11-13 feat: Add partial BOM
2023-11-28 fix: Add feet holes around all sides of Vertical supports
    [BackLeftVerticalSupport.SLDPRT, BackLeftVerticalSupport.stl, BackRightVerticalSupport.SLDPRT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]
2023-11-28 feat: Add current build photos
2023-12-04 feat: First images of milled frame piece
2023-12-12 chore: Solidworks 2024
    [BackLeftVerticalSupport.SLDPRT, BackLeftVerticalSupportAssembly.SLDASM, BackRightVerticalSupport.SLDPRT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]
2023-12-15 fix: Mill stepper hole with .25". Remove trailing carriage returns
2023-12-18 fix: speeds and feeds. Pre-drill
2023-12-20 fix: Incorrect Y position used for stepper hole & remove commented holes
2024-01-01 fix: A hole in the wrong direction
2024-01-07 feat: Add in current frame assembly status
2024-01-11 feat: Add holes to make it easier to access linear guide block fasteners
    [LeftGantryBlock.SLDPRT, RightGantryBlock.SLDPRT]
2024-01-11 fix: SolidWorks 2024 suddenly made three holes bigger than they were supposed to be
    [FrontLeftVerticalSupport.SLDPRT]
2024-01-19 fix: The 1/8th stepper hole should be the same center as the 1/4 drill bit
2024-01-22 Fix: Resolve screw collisions during frame assembly
    [BackLeftVerticalSupport.SLDPRT, BackLeftVerticalSupportAssembly.SLDASM, BackRightVerticalSupport.SLDPRT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]
2024-01-23 fix: Belt tensioner mounting hole diameter increased from 3.5 to 4mm to accept M4 screw
    [FrontLeftVerticalSupport.SLDPRT, FrontLeftVerticalSupportAssembly.SLDASM, FrontRightVerticalSupport.SLDPRT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]
2024-01-24 feat: Add lower enclosure for future electronics
    [BackLeftVerticalSupport.SLDPRT, BackLeftVerticalSupport.stl, BackLeftVerticalSupportAssembly.SLDASM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]
2024-02-08 feat: Stengthen MidSideRail to 2in. Stengthen RodStabilizer for future larger Y Axis build. Add lower enclosure to mount electronics. Continue screw collision fixes.
    [24V15A.SLDASM, BackLeftVerticalSupport.SLDPRT, BackLeftVerticalSupport.stl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]
2024-02-08 feat: Remove unnecessary upper corner block
    [BackLeftVerticalSupportAssembly.SLDASM, BackRightVerticalSupport.SLDPRT, BackRightVerticalSupportAssembly.SLDASM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]
2024-02-10 feat: Lower enclosure electronics
    [24V15A.SLDASM, BedAssembly.SLDASM, BedBL.SLDPRT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]
2024-02-12 docs: Update README/Changelog ...
    [LowerEnclosure.SLDPRT, LowerEnclosureAssembly.SLDASM, XAxisLinearRailAssembly.SLDASM]
2024-02-18 fix: BeltTensioner around midrail mounting screws and make midbackrail steppers face upwards for cable routing and lower center of balance
    [BackLeftVerticalSupport.SLDPRT, BackLeftVerticalSupportAssembly.SLDASM, BackRightVerticalSupport.SLDPRT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]
2024-02-18 fix BeltTensioners to fit around mid rail mounting screws and change bed center from a solid to a shell
    [BackLeftVerticalSupportAssembly.SLDASM, BackRightVerticalSupportAssembly.SLDASM, BedAssembly.SLDASM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]
2024-02-19 chore: update NC files and STL files accordingly
    [BackLeftVerticalSupport.stl, BackRightVerticalSupport.stl, FrontLeftVerticalSupport.STL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]
2024-02-21 fix: Change RodStabilizer and Bed/Build plate holes to accept M3 Heat insert.
    [BedAssembly.SLDASM, BedBL.stl, BedBR.SLDPRT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]
2024-03-01 fix: Proof equations after flipping back mid rail steppers to face upwards. Change fastening holes from 4 to 3 to accommodate screw heads.
    [6-32By.5.SLDPRT, 6-32By3-8.SLDPRT, 6-32By5-8.SLDPRT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]
2024-03-01 feat: add frame screws. Update STL files
    [BackLeftVerticalSupport.stl, BackRightVerticalSupport.stl, Carrier.stl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]
2024-03-16 fix: Change to 1 foot mount hole on vertical rails. Add fastening screws to frame
    [BackLeftVerticalSupport.SLDPRT, BackLeftVerticalSupport.stl, BackLeftVerticalSupportAssembly.SLDASM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]
2024-03-20 fix: Proper holes for mid back rail on verticals. Found after machining :-(
2024-03-22 fix: Add M3HeatInsertHoleSize. Make sure stl files are correct before print
    [BedBL.SLDPRT, BedBL.stl, BedBR.SLDPRT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]
2024-03-22 fix: something funny with last commit. Accidentally saved STL file over SLDPRT file for RodStabilizer somewhere along the way
    [BedBL.SLDPRT, BedBR.SLDPRT, BedFL.SLDPRT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]
2024-03-24 fix: Move MidBackRail steppers forward to access back corner stepper screw
    [BedAssembly.SLDASM, MidBackRail.SLDPRT, MidBackRail.stl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]
2024-03-24 fix: Change NC files for last commit
    [MidBackRail.SLDPRT]
2024-03-30 fix: Round over belt tensioner corner to fit inside verticals
    [LeftBeltTensioner.SLDPRT, LeftBeltTensioner.stl, RightBeltTensioner.SLDPRT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]
2024-04-01 fix: Add counter sink to gantry block mounting holes
    [LeftBeltTensionerAssembly.SLDASM, LeftGantryBlock.SLDPRT, LeftGantryBlock.stl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]
2024-04-02 fix: Increase size of Gantry block access holes. Add new hole for future X-Axis Rail support
    [LeftGantryBlock.SLDPRT, LeftGantryBlock.stl, LeftGantryBlockAssembly.SLDASM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]
2024-04-03 feat: Add cable holes to. lower frame
    [LowerBackRail.SLDPRT, LowerBackRail.stl, LowerEnclosure.SLDPRT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]
2024-04-06 feat: Mount X-Axis linear rail on its own printed bar
    [LeftGantryBlockAssembly.SLDASM, LeftXAxisLinearRailSupport.SLDPRT, LeftXAxisLinearRailSupport.STL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]
2024-04-18 feat: Add XAxis linear rail support. Show start of wiring
    [LeftXAxisLinearRailSupport.SLDPRT, LeftXAxisLinearRailSupport.STL, RightXAxisLinearRailSupport.SLDPRT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]
2024-04-23 feat: Reduce weight of Carrier
    [Carrier.SLDPRT, Carrier.stl]
2024-04-24 feat: ZAxis endstop plus future ZAxis lifters to replace bed. Reduce weight of Carrier
    [FrontLeftVerticalSupport.SLDPRT, FrontLeftVerticalSupport.STL, FrontLeftVerticalSupportAssembly.SLDASM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]
2024-04-24 doc: Update Changelog for last commit of also BeltFastener mod
2024-04-25 feat: XAxis stops to left rear endstop
    [RodStabilizerPlusXZStops.SLDPRT, RodStabilizerPlusXZStops.STL, RodStabilizerPlusZStop.SLDPRT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]
2024-06-14 feat: Update project documentation and files for current status
    [BigTreeHDMI7Case.SLDPRT, BigTreeHDMI7Case.STL, HDMI Mount.SLDPRT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]
2024-06-15 doc: Update Wiring build photo
    [HDMI7 Case.STL]
2024-06-16 fix: Mid mounting hole on wrong side. Tighten USB connector placement
    [BigTreeHDMI7Case.SLDPRT, BigTreeHDMI7Case.STL]
2024-06-17 fix: USBC connectors fit perfectly now
    [BigTreeHDMI7Case.SLDPRT, BigTreeHDMI7Case.STL]
2024-06-27 Create Gotchas documentation and update wiring clamps
    [EndStopRibbonCableCornerClamp.SLDPRT, EndStopRibbonCableCornerClamp.STL, NRibonnCableCornerClamp.SLDPRT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]
2024-07-11 fix: Flush connectors with HDMi case, Correct schematic with Octopus, cable clamp had sketch entity hidden
    [BigTreeHDMI7Case.SLDPRT, BigTreeHDMI7Case.STL, EndStopRibbonCableCornerClamp.SLDPRT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]
2024-07-11 fix: Spacing around flange nut
    [ShortBedSupport.SLDPRT, ShortBedSupport.STL]
2024-07-12 fix: minor HDMI and USB connector alignment for print
    [BigTreeHDMI7Case.SLDPRT, BigTreeHDMI7Case.STL]
2024-09-08 fix: Update files for what is close to Alpha4
    [6-32By.5.SLDPRT, 6-32By3-8.SLDPRT, 6-32By5-8.SLDPRT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]
2024-09-09 fix: Began bedAssembly2 and end stops to back right.
    [BedAssembly2.SLDASM, BuildPlate.SLDPRT, LeftGantryBlock.SLDPRT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]
2024-09-11 fix. Add endstops to back right
    [BedAssembly.SLDASM, BedAssembly2.SLDASM, LeftGantryBlockAssembly.SLDASM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]
2024-09-28 feat: Change bed to ball joints
    [RightXAxisEndStopSupport.SLDPRT, RightXAxisEndStopSupport.STL, RodStabilizerPlusRightZStop.SLDPRT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]
2024-10-14 feet: Add in probe mounts. Tweek endstops
    [BLTouchProbeMount.SLDPRT, BLTouchProbeMount.STL, BuildPlateZEndStopHolder.SLDPRT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]
2024-11-17 Update to Alpha 5 for metal bed
    [Bed3.SLDPRT, Bed3.STL, BedAssembly1.SLDASM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]
2025-02-17 Fix: Just about everything redesigned/rebuilt to solve bed levelling.
    [AC Power Inlet.SLDPRT, AC Power Inlet.stp, AngleBracket.SLDPRT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]
2025-03-24 feat: Redesign to fix bed leveling
    [Bed.SLDPRT, BedAssembly.SLDASM, Carrier.SLDPRT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]
2025-03-27 test: Adding RatOS config files for testing
    [My100350.cfg, My100Steppers.cfg, caselight.cfg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]
2025-03-28 fix: Update to actual connections
    [LowerEnclosure.SLDPRT, LowerEnclosureAssembly.SLDASM]
2025-03-29 dpcs" Straighten and shorten a few cables
2025-04-10 fix: Bed Mesh, larger Z End Stop
    [BedAssembly.SLDASM, BuildPlateZEndStopHolderAssembly.SLDASM, BuildPlateZEndStopHolderWithMicroSwitchAssembly.SLDASM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]
2025-04-28 fix: extruder dir_pin. Move gantry steppers to electronics levlr reducing possible heat affects
    [BuildPlateWithGlassPlateZEndStopSwitchHolder.SLDPRT, BuildPlateWithGlassPlateZEndStopSwitchHolder.STL, Carrier.SLDPRT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]
2025-05-01 fix: Make Y endstop adjustable. Update main assembly pic
    [MidRightRailAssembly.SLDASM, YAxisEndStopBaseForRightRearSK8RodHolder.SLDPRT, YAxisEndStopBaseForRightRearSK8RodHolder.STL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]
2025-05-05 fix: Make end stop microswitch holder work for both X&Y axis. Also add sliding guide to both of them. Lower probe 2.5mm on carrier.
    [Carrier.SLDPRT, Carrier.STL, HotEndAssembly.SLDASM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]
2025-05-09 fix: Add SK8Risers, Use common end stop micro switch holder. Add platform to carrier for probe
    [Carrier.SLDPRT, HotEndAssembly.SLDASM, InductiveProbe.SLDPRT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]
2025-05-09 doc: Update electronics image with shortened cables.
